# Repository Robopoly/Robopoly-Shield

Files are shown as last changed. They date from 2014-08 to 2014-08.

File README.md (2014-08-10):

# Robopoly Shield

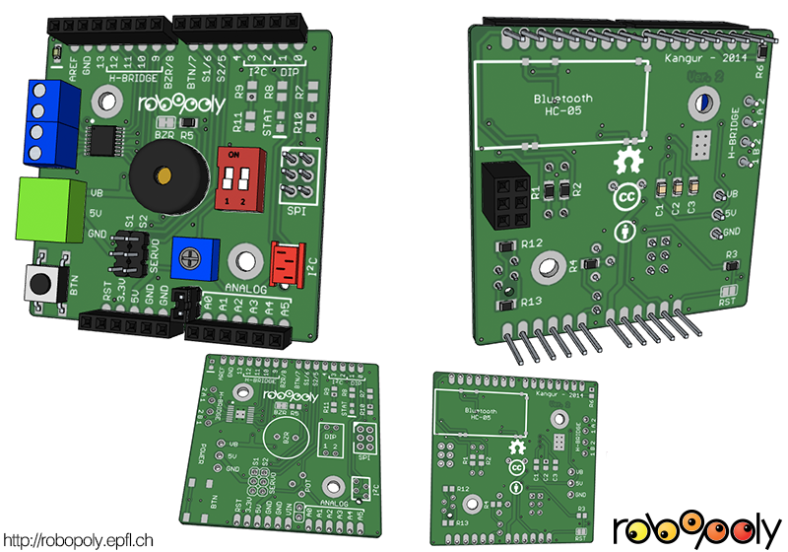
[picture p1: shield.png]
Robopoly shield


This Arduino compatible shield is intended to work with the [EPFL Robotics club (Robopoly)](http://robopoly.epfl.ch) robotics platform: the [PRismino](https://github.com/Robopoly/PRismino). It can run on any Arduino as the pin placement is the same. The [PRismino library](https://github.com/Robopoly/prismino-library) makes it easy to use with shortcut definitions and functions.

It's main purpose is to augment the PRismino's capabilities, Robopoly organises [mobile robotics challenges](http://robopoly.epfl.ch/evenements) each year and provides all components in a form of [disassembled kit](http://robopoly.epfl.ch/prisme) including motors and sensors. The H-bridge is one of the most important components as the is allows to build a differential wheeled mobile robot.

Tests have been carried out to see the robustness of the H-bridge, it has an overtemperature shutdown function and short-circuit protection which proved reliable.

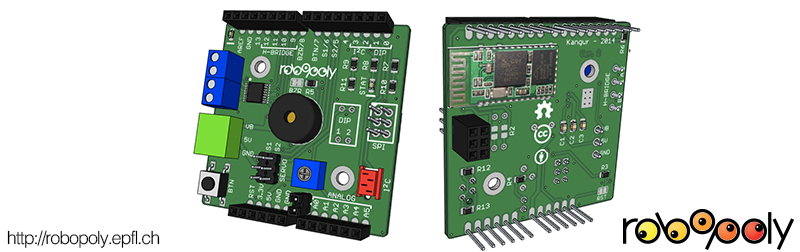
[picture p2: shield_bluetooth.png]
Robopoly shield with Bluetooth module installed


Robopoly shield with Bluetooth module installed instead of the DIP-switch.

## Characteristics

The shield has various input and output components to expand the PRismino's capabilities:

* Push button, can be used as a regular button (attached to an interrupt pin) or as reset button
* 2 channel DIP-switch
* 2 standard servo motor connections
* SPI port
* Buzzer
* 2 channel H-bridge with connectors ([DRV8833](http://www.ti.com/product/drv8833))
* Potentiometer, can be disabled by removing a jumper
* [I<sup>2</sup>C](http://en.wikipedia.org/wiki/I%C2%B2C) output with a micromatch connector
* Footprint for a HC-05 Bluetooth module
* 3-pin connector for power from the [Robopoly power board](https://github.com/Robopoly/Power-Board)

**NOTICE**: certain components that source current are wired to the micro-controller pins and **may damage it if those pins are configured as outputs**, please read carefully the [PRsimino library documentation](https://github.com/Robopoly/prismino-library) to avoid it.

The button can serve as a reset button or an interrupt button.

The DIP-switch shares the same pins as the serial pins, so the Bluetooth module cannot be used when the DIP-switch is used.

There's an absolute maximum rating of 11.8V on the VB input because of the H-bridge.

## Electrical schematic and PCB

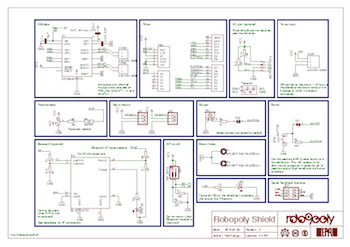
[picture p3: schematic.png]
Electrical schematic

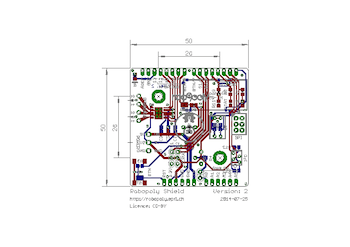
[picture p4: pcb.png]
PCB


## Assembly

The assembly of the Robopoly shield is [documented on the Robopoly's website](http://robopoly.epfl.ch/prisme/assemblage).

## Usage

Refer to the [PRsimino library](https://github.com/Robopoly/prismino-library) and [Bluetooth library](https://github.com/Robopoly/bluetooth-library) for documentation.

The pins 0 and 1 source current, so they shouldn't be used as outputs at any time. Other pins are used for various things but do not put the micro-controller in danger when used as outputs.

| Pin | Function | Comments |
| --- | --- | --- |
|`A0` | Potentiometer, can be disabled | Protected by a 10K in-line resistor |
|`A1` | | |
|`A2` | | |
|`A3` | | |
|`A4` | | |
|`A5` | | |
|`0`  | DIP-Switch/UART RX (Bluetooth) | Do not use as output |
|`1`  | DIP-Switch/UART TX (Bluetooth) | Do not use as output |
|`2`  | I<sup>2</sup>C SDA | Can use internal or external pull-up resistor |
|`3`  | I<sup>2</sup>C SCL | Can use internal or external pull-up resistor |
|`4`  | Bluetooth module AT mode selector | Enters Bluetooth module configuration mode when mounted |
|`5`  | Servo motor | Use `S1` in program when addressing the pin |
|`6`  | Servo motor | Use `S2` in program when addressing the pin |
|`7`  | Button | Protected by a 10K in-line resistor, use internal pull-up resistor |
|`8`  | Buzzer | Disable via solder jumper to use as input |
|`9`  | H-bridge | Can be used for anything as long as the H-bridge is not used |
|`10` | H-bridge | Can be used for anything as long as the H-bridge is not used |
|`11` | H-bridge | Can be used for anything as long as the H-bridge is not used |
|`12` | H-bridge | Can be used for anything as long as the H-bridge is not used |
|`13` | LED | Do not use as input as it will consume power |

## Component list

The quantity indicates the number of components needed when using the DIP-switch or when using the Bluetooth module. In parenthesis are the 2 10K pull-up resistors for the I<sup>2</sup>C, since the micro-controller has internal pull-up resistors they are optional.

| Part | Reference | Quantity  |
| --- | --- | --- |
| PCB | | 1 |
| H-bridge (HTSSOP-16) | DRV8833 | 1 |
| 10uF (minimum) ceramic capacitor | | 1 |
| 10nF, 16V (minimum), X7R, ceramic capacitor | | 1 |
| 2.2uF, 6.3V, 0805 capacitor | | 1 |
| H-bridge connectors | 4UCON-19963 | 2 |
| DIP switch with 2 switches (red) | 4UCON-07236 | 1 |
| SPI 2x3 stackable header | 4UCON-18677 | 1 |
| 10K 0805 resistor | | 4(2)/2(2) |
| 6 pin stackable header (10.5mm) | 4UCON-18688 | 2 |
| 8 pin stackable header (10.5mm) | 4UCON-18689 | 2 |
| Button | | 1 |
| 3 male pins for servo motors | 4UCON-19631 | 2 |
| 3 pin power connector male | 4UCON-19836 | 1 |
| 3 pin power connector female | 4UCON-19841 | 1 |
| Buzzer | | 1 |
| 1K 0805 resistor | | 2/5 |
| Potentiometer 10K | | 1 |
| 2x1 male pins for potentiometer | 4UCON-00795 | 1 |
| Jumper/shunt for potentiometer (6mm, blue) | 4UCON-05726 | 1 |
| Bluetooth module HC-05 | HC-05 | 0/1 |
| 2K 0805 resistor | | 0/2 |
| SMD LED 0805 | | 1/2 |
| Micromatch 4 pin connector | 7-215079-4  | 1 |

## CAD files

The CAD file is in [Google Sketchup](http://www.sketchup.com) format. Generated with [eagleUp](http://eagleup.wordpress.com/), a plugin that exports the board from [Eagle CAD](http://www.cadsoftusa.com) and imports it to Google Sketchup.

All additional files needed to generate the board are in the [Robopoly Eagle CAD library and SketchUp files](https://github.com/Robopoly/Robopoly-Eagle-library) project.

## Version log

### 2.0 (2014-07-25)

* Added information about pin usage on silkscreen.
* Added an optional LED on pin 13 since the one on the PRismino is hidden by the shield.
* Replaced potentiometer solder jumper with an actual jumper to free `A0` pin for other functions.
* Moved button pull-up resistor in series with the line for short-circuit protection, the micro-controller internal pull-up shall be used instead.
* Added a resistor in series with the potentiometer line for short-circuit protection.
* Renamed passive elements silkscreen information in order in which they should be soldered.
* Changed DIP-switch to a 2 channel switch instead of 4.
* Added a stackable SPI header for future module developments.
* The buzzer solder jumper is now connected by default.
* Rounded corners.
* Updated CAD and Gerber files.
* Updated version number and year.
* Added component list.

### 1.0 (2013-07-09)

* Initial version.

## Licence

The Robopoly shield is published under [Creative Commons Attribution license](http://creativecommons.org/licenses/by/3.0/).



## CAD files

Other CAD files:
cad.skp

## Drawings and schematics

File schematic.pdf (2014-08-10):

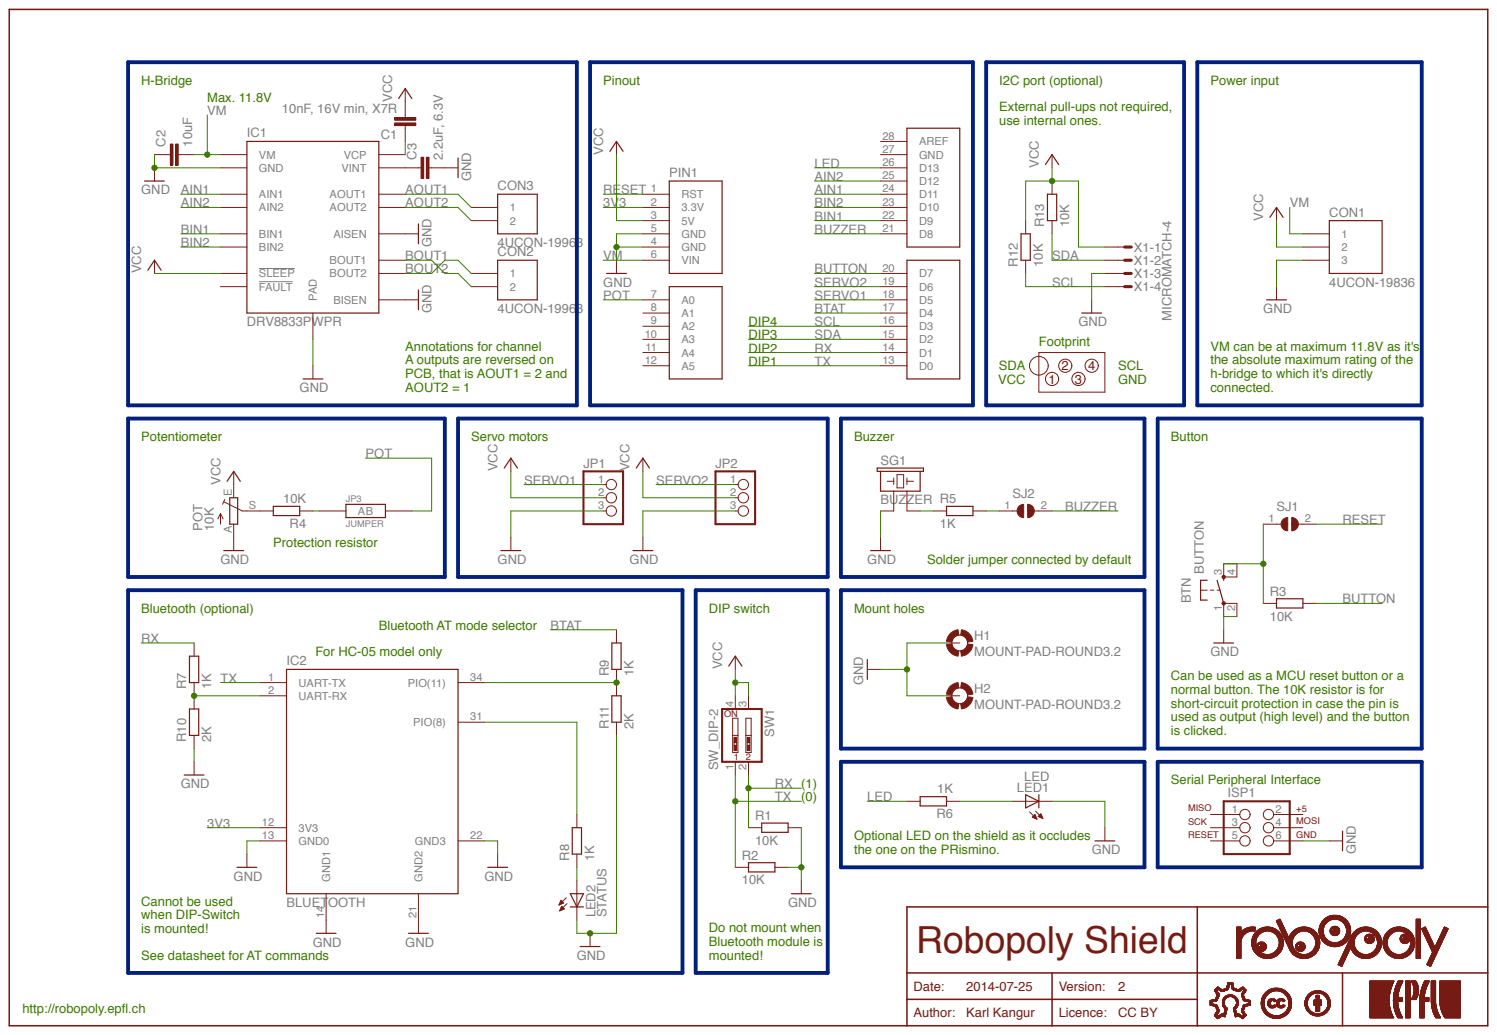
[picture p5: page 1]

External pull-ups not required,
use internal ones.

Annotations for channel
A outputs are reversed on
PCB, that is AOUT1 = 2 and
AOUT2 = 1

VM can be at maximum 11.8V as it's
the absolute maximum rating of the
h-bridge to which it's directly
connected.

Solder jumper connected by default

Bluetooth AT mode selector

For HC-05 model only
UART-TX 1
UART-RX 2

Can be used as a MCU reset button or a
normal button. The 10K resistor is for
short-circuit protection in case the pin is
used as output (high level) and the button
is clicked.

Optional LED on the shield as it occludes
the one on the PRismino.

Robopoly Shield

See datasheet for AT commands

Date: 2014-07-25 | Version: 2

http://robopoly.epfl.ch

Author: Karl Kangur | Licence: CC BY

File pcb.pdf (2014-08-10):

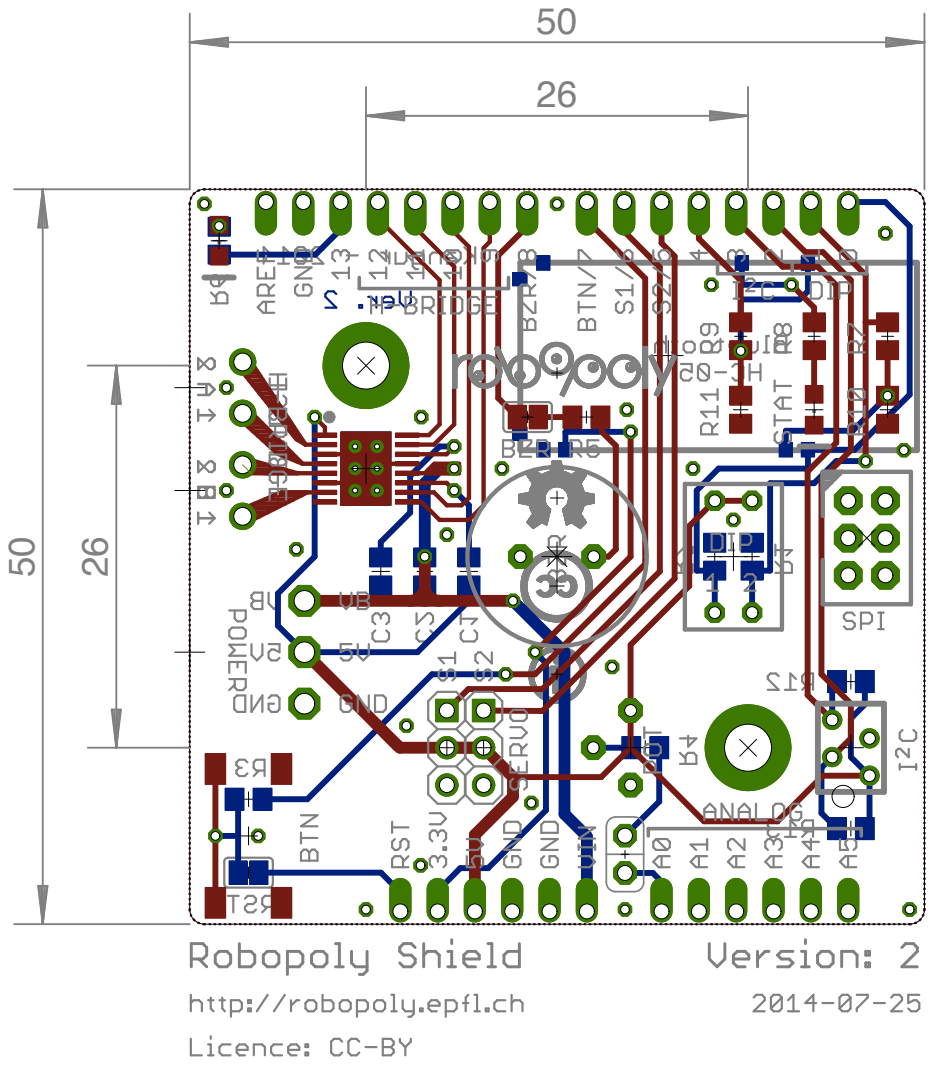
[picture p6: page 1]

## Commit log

2014-02-07 Updated everything
    [cad.skp, robopoly_shield.brd]
2014-02-10 Replaced 4 channel DIP-switch with 2 and added stackable SPI header
    [cad.skp, robopoly_shield.brd]
2014-07-25 Final update for this version... probably
    [cad.skp, robopoly_shield.brd]
